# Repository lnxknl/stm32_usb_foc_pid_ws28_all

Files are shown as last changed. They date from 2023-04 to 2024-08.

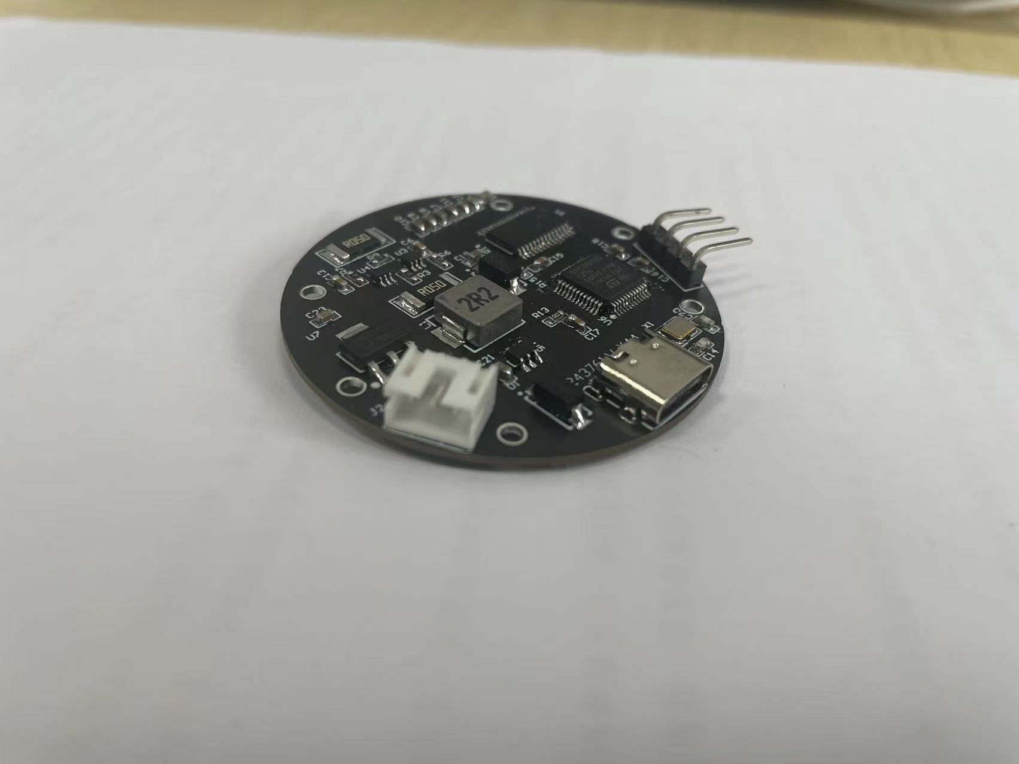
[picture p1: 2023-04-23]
4.Image/pcb侧面图.jpg

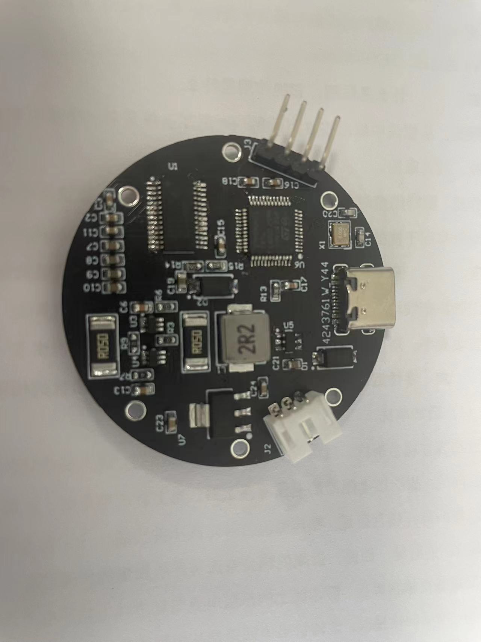
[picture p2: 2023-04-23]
4.Image/pcb正面图.jpg

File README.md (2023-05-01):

**求个START**

## 一. 硬件设计

**主控** : STM32G431CBT6

**稳压芯片**: AMS1117-3.3

**升压芯片**: MT3608(5V升压12V,最大电流支持2A)

**电流采样芯片**: INV199A1DCKR(两相)

**电机驱动芯片**: DRV8313

采用type-c接口供电以及进行usb通讯，2.54弯针接口进行ST-Link下载程序，另外提供了一个PH2.0-3接口(本人用来驱动ws2812)，采用两层板设计。

pcb描述图-反面

pcb描述图-正面

整体图

## 二. 软件设计

##### (1).STM32平台软件设计

###### 1. AS5600参数校准

通过IIC接口读取0x0F和0x0E两个寄存器，可以得到电机的机械角度，此时电机的零角度与AS5600读出的零角度可能不对应，需要进行校准。

将电机旋转到你预想0°的位置，设置foc角度为0°，可以将Ud设置大一点，然后上电，可以看到电机有个微小的偏移，此时读出AS5600的角度值X1，作为**机械角度零偏值**。然后将foc角度设置为90°，上电，再次读出AS5600的角度值X2，那么就可以确定电机的**极对数** = (360 / ((X2 -X1)*4))。电角度和机械角度的转换关系就可以确定下来了。

###### 2. USB协议设计

与PC平台通讯将采用HID复合设备的显示，共两个接口。

第一个为自定义的HID，每个数据包为8bytes，用来进行数据交互。

第二个为HID键盘，配合电机可以发送一些对应的按键，例如: 暂停、切歌、调节音量等等。

##### (2). QT平台软件设计

###### 1. USB协议

采用开源库hidapi进行设计，通过PID和VID锁定设备，然后对接口0进行读写，接口1不管。

###### 2. 串口协议

同样支持通过串口进行交互

###### 2. OpenGL 电机模型

采用OpenGL库读取电机3D模式obj文件，然后将其显示在界面中，与电机旋转位置保持一致。

##### (3).  通讯协议

一个数据包为8字节，首字节恒为0xef，尾字节恒为0xab，中间六个字节为有效数据部分。

###### 1. 公共参数

上位机发送

| 功能码 | 参数码 | 数值4 | 数值3 | 数值2 | 数值1 |
| :----: | :---: | :---: | :---: | :---: | :---: |
|  0x12  | 0x20(运行模式) | 0 | 0 | 0 | 模式 |
|  0x12  | 0x2a(Uq) | float高位 | float低三位 | float低二位 | float低位 |
|  0x12  | 0x2b(Ud) | float高位 | float低三位 | float低二位 | float低位 |
|  0x12  | 0x2c(速度) | float高位 | float低三位 | float低二位 | float低位 |

上位机接收

| 功能码 | 参数码 | 数值4 | 数值3 | 数值2 | 数值1 |
| :----: | :---: | :---: | :---: | :---: | :---: |
|  0x14  | 0x2a(Uq) | float高位 | float低三位 | float低二位 | float低位 |
|  0x14  | 0x2b(Ud) | float高位 | float低三位 | float低二位 | float低位 |
|  0x14  |  0x2c(速度)  | float高位 | float低三位 | float低二位 | float低位 |
|  0x14  |  0x2d(角度)  | float高位 | float低三位 | float低二位 | float低位 |
|  0x14  | 0x2e(Iq电流) | float高位 | float低三位 | float低二位 | float低位 |
|  0x14  | 0x2f(Id电流) | float高位 | float低三位 | float低二位 | float低位 |

##### 2. 位置控制

上位机发送

| 功能码 | 参数码 | 数值4 | 数值3 | 数值2 | 数值1 |
| :----: | :---: | :---: | :---: | :---: | :---: |
|  0x22  | 0x1a(设置角度) | 0 | 0 |  角度高8位  | 角度低8位 |
|  0x22  |  0x1b(设置P) | float高位 | float低三位 | float低二位 | float低位 |
|  0x22  |  0x1c(设置I) | float高位 | float低三位 | float低二位 | float低位 |
|  0x22  |  0x1d(设置D) | float高位 | float低三位 | float低二位 | float低位 |

上位机接收

| 功能码 | 参数码 | 数值4 | 数值3 | 数值2 | 数值1 |
| :----: | :---: | :---: | :---: | :---: | :---: |
|  0x24  | 0x1b(接收P) | float高位 | float低三位 | float低二位 | float低位 |
|  0x24  | 0x1c(接收I) | float高位 | float低三位 | float低二位 | float低位 |
|  0x24  | 0x1d(接收D) | float高位 | float低三位 | float低二位 | float低位 |

##### 3. 开环控制

上位机发送

| 功能码 | 参数码 | 数值4 | 数值3 | 数值2 | 数值1 |
| :----: | :---: | :---: | :---: | :---: | :---: |
|  0x32  | 0x1a(设置运动方向) | 0 | 0 | 0 | 方向(0-顺时针，1-逆时针) |

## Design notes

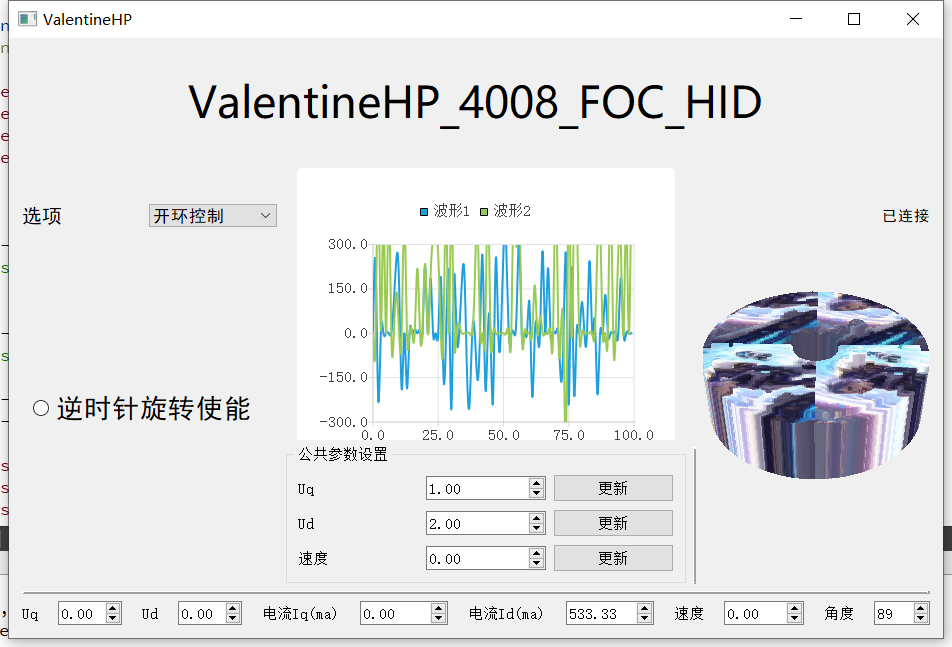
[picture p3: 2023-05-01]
4.Image/上位机.png

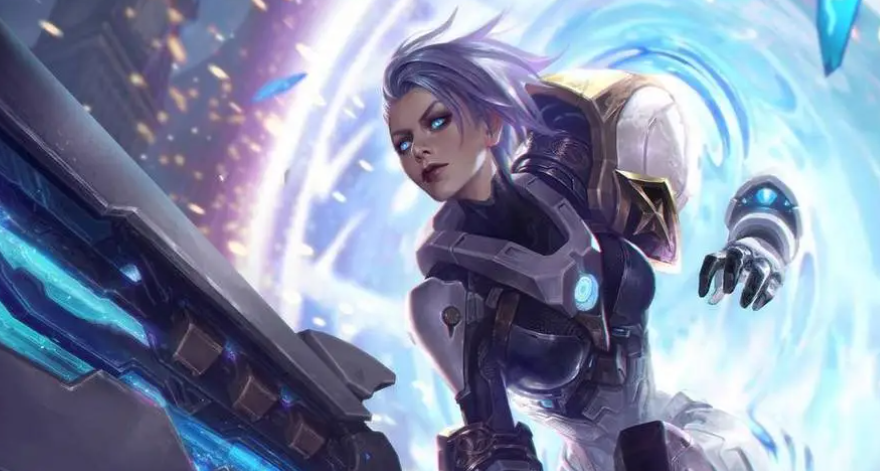
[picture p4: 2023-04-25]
3.Software/QT_FOC_HID/model/tup.png

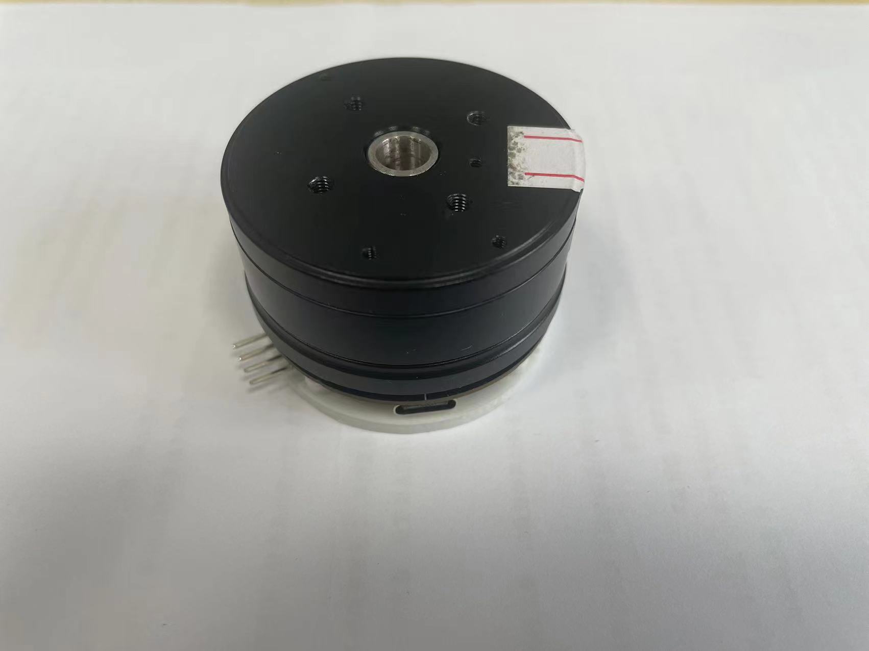
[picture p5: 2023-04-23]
4.Image/整体图.jpg

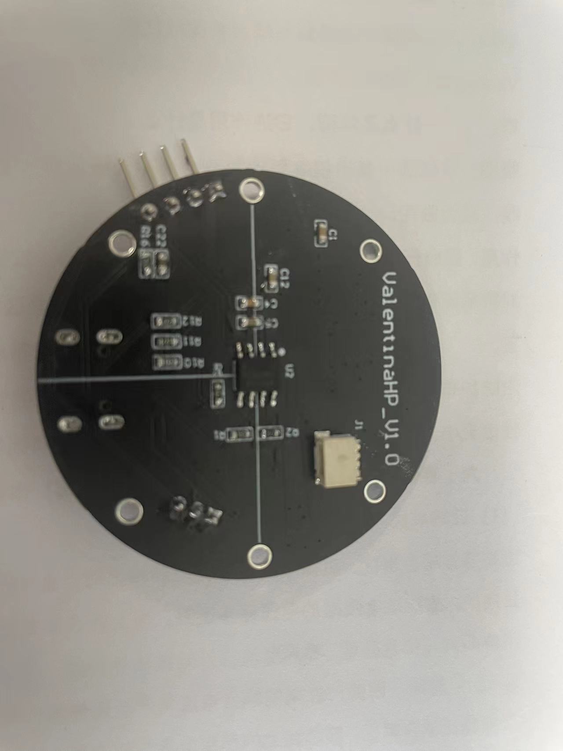
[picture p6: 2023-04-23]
4.Image/pcb背面图.jpg

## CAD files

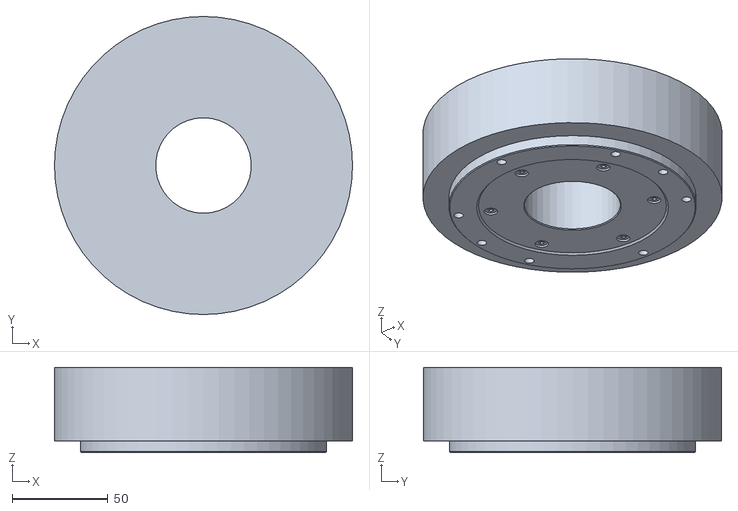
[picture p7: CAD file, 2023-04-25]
2.SolidWorks/SGMCS-04C3C11 - SGMCS-04C3C11.step-1 SGMCS__-4__14N__m-_____04.step.step-1.STL
156.0 x 156.0 x 44.5

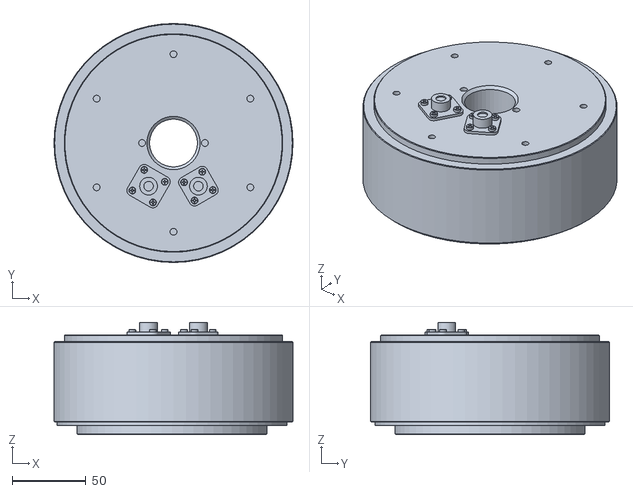
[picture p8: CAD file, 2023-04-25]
3.Software/QT_FOC_HID/model/motor.obj
162.2 x 162.2 x 76.0

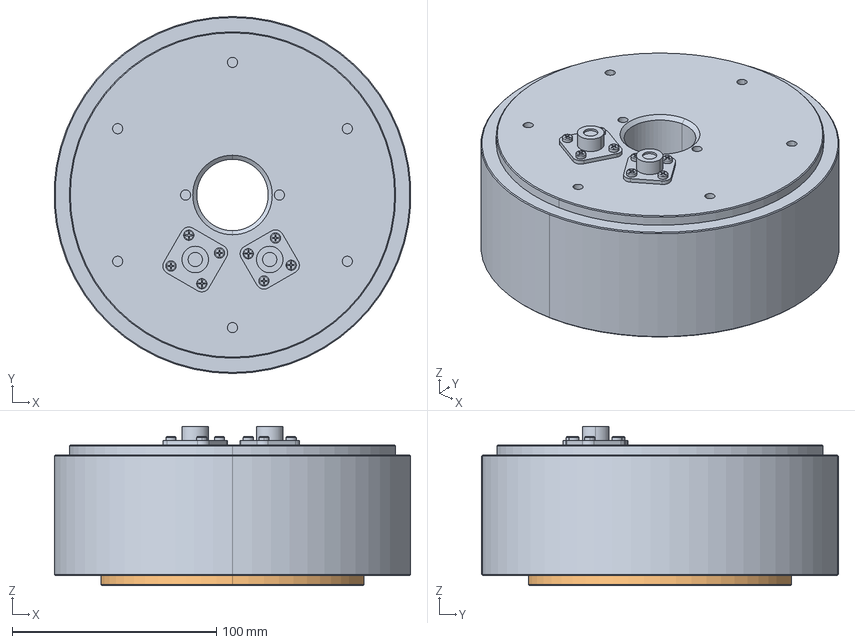
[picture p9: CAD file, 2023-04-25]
2.SolidWorks/SGMCS-04C3C11.step
174.7 x 175.0 x 78.0 mm
SGMCSﾐﾍ-4｡ｫ14N｡､m-ｶｨﾗﾓ_1_04.step
SGMCSﾐﾍ-4｡ｫ14N｡､m-ﾗｪﾗﾓ_04.step

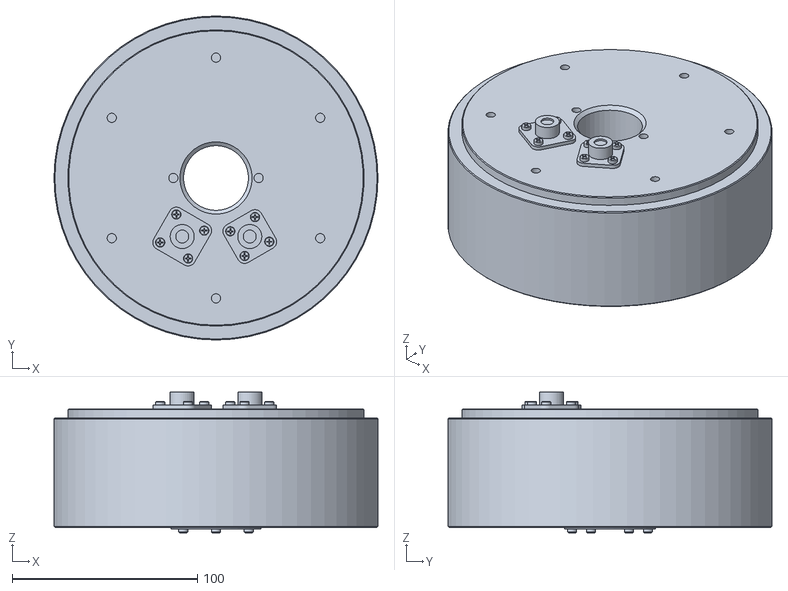
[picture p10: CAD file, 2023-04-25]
2.SolidWorks/SGMCS-04C3C11 - SGMCS-04C3C11.step-1 SGMCS__-4__14N__m-_____1_04.step.step-1.STL
175.0 x 175.0 x 76.0

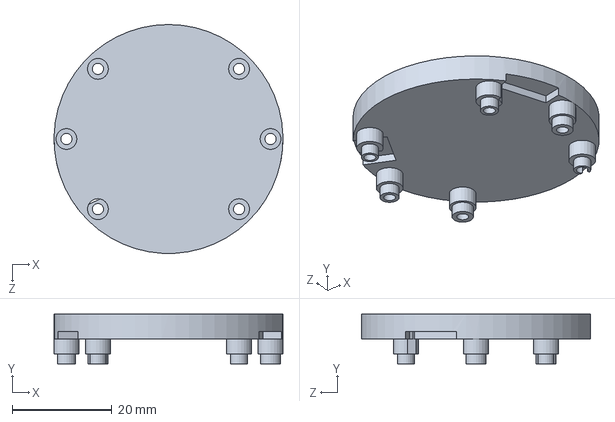
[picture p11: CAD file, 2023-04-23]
2.SolidWorks/4008云台电机外壳.SLDPRT
46.0 x 10.0 x 46.0 mm

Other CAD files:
2.SolidWorks/4008云台电机外壳.STL
2.SolidWorks/SGMCS-04C3C11.SLDASM

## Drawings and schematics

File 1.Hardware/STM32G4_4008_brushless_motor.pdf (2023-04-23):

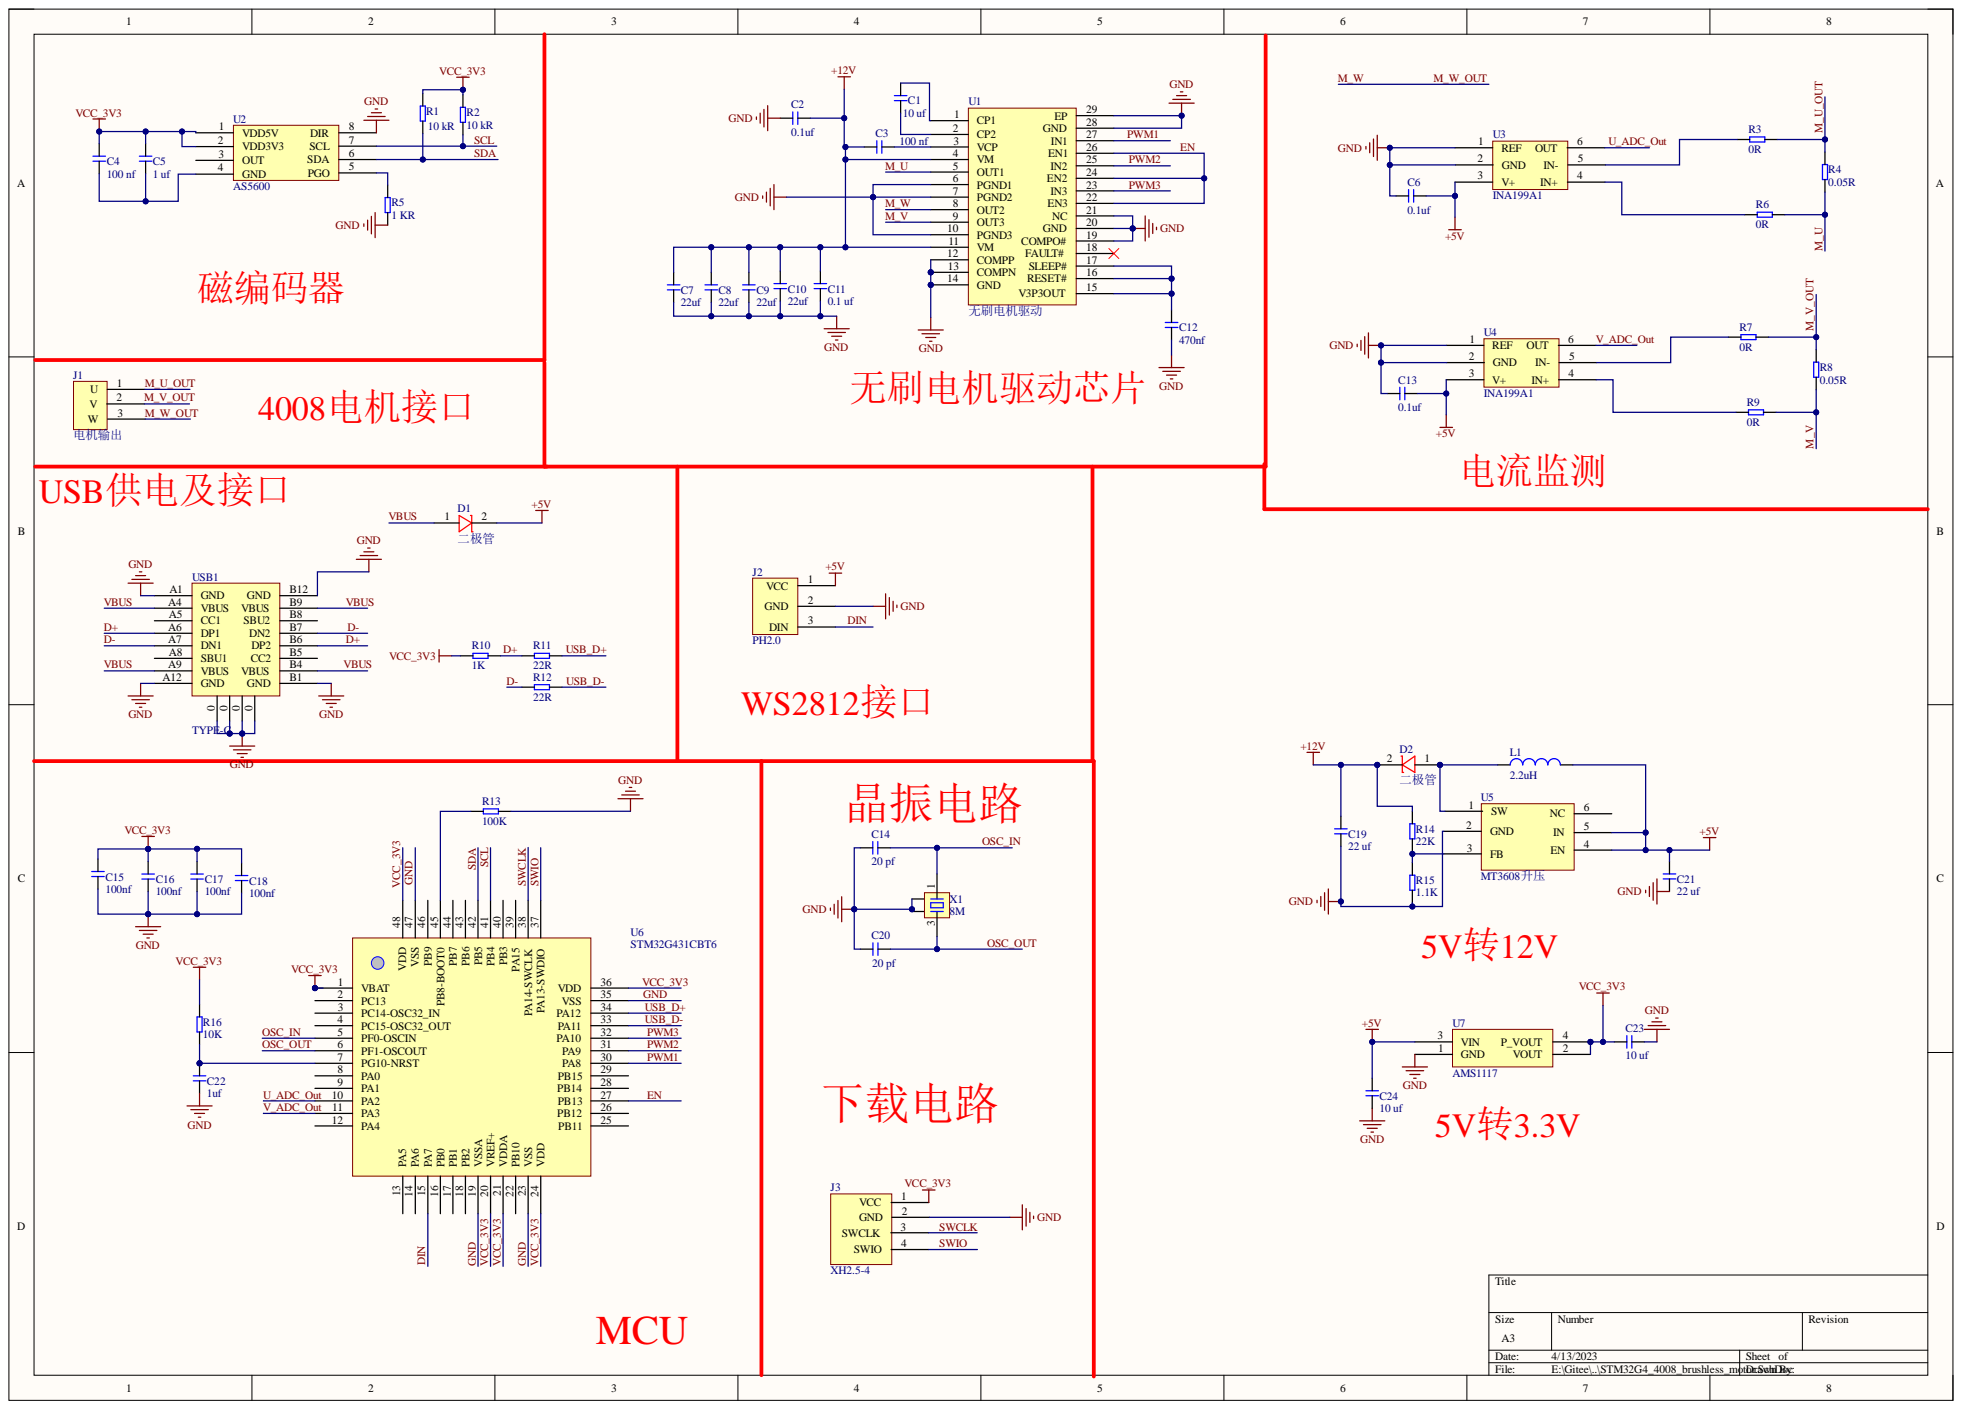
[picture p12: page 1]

PGND1 6 | PWM3
PGND2 7

M_W | OUT2 8

PA13-SWDIO 37 PA14-SWCLK 38 PA15 39 PB3 40 PB4 41 PB5 42 PB6 43 PB7 44 PB8-BOOT0 45 PB9 46 VSS 47 VDD 48

PG10-NRST 7 | PWM1
PA0 8 | EN

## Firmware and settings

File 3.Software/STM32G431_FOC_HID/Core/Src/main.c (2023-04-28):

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
/* Includes ------------------------------------------------------------------*/
#include "main.h"
#include "adc.h"
#include "dma.h"
#include "tim.h"
#include "usart.h"
#include "usb_device.h"
#include "gpio.h"

/* USER CODE BEGIN Includes */
//#include "usbd_cdc_if.h"
/* USER CODE END Includes */

/* USER CODE BEGIN PTD */
#include "common_inc.h"
/* USER CODE END PTD */


void SystemClock_Config(void);
/**
  * @brief  The application entry point.
  * @retval int
  */
int main(void)
{
  /* MCU Configuration--------------------------------------------------------*/

  /* Reset of all peripherals, Initializes the Flash interface and the Systick. */
  HAL_Init();

  /* Configure the system clock */
  SystemClock_Config();

  /* USER CODE BEGIN SysInit */
  GPIO_InitTypeDef GPIO_InitStruct = {0};
  __HAL_RCC_GPIOA_CLK_ENABLE();
  HAL_GPIO_WritePin(GPIOA, GPIO_PIN_12, GPIO_PIN_RESET);
  GPIO_InitStruct.Pin = GPIO_PIN_12;
  GPIO_InitStruct.Mode = GPIO_MODE_OUTPUT_PP;
  GPIO_InitStruct.Pull = GPIO_NOPULL;
  GPIO_InitStruct.Speed = GPIO_SPEED_FREQ_MEDIUM;
  HAL_GPIO_Init(GPIOA, &GPIO_InitStruct);
  HAL_GPIO_WritePin(GPIOA, GPIO_PIN_12, GPIO_PIN_RESET);
  /* USER CODE END SysInit */

  /* Initialize all configured peripherals */
  MX_GPIO_Init();
  MX_DMA_Init();
  MX_USB_Device_Init();
  MX_ADC1_Init();
  MX_TIM1_Init();
  MX_TIM2_Init();
  MX_TIM3_Init();
  MX_USART3_UART_Init();
  /* USER CODE BEGIN 2 */
  HAL_Delay(1000);
  AppMain();
  /* USER CODE END 2 */

  /* Infinite loop */
  /* USER CODE BEGIN WHILE */
  while (1)
  {
    /* USER CODE END WHILE */

    /* USER CODE BEGIN 3 */
  }
  /* USER CODE END 3 */
}

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


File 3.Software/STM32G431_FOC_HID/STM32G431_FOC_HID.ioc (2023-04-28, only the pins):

Mcu.UserName=STM32G431CBTx
PA10.Signal=S_TIM1_CH3
PA11.Signal=USB_DM
PA12.Signal=USB_DP
PA13.Signal=SYS_JTMS-SWDIO
PA14.Signal=SYS_JTCK-SWCLK
PA2.Signal=ADC1_IN3
PA3.Signal=ADC1_IN4
PA7.GPIO_Label=Dout
PA7.Signal=GPIO_Output
PA8.Signal=S_TIM1_CH1
PA9.Signal=S_TIM1_CH2
PB10.Signal=USART3_TX
PB11.Signal=USART3_RX
PB13.GPIO_Label=FOC_Enable
PB13.Signal=GPIO_Output
PB4.GPIO_Label=AS5600_SCL
PB4.Signal=GPIO_Output
PB5.GPIO_Label=AS5600_SDA
PB5.Signal=GPIO_Output
PF0-OSC_IN.Signal=RCC_OSC_IN
PF1-OSC_OUT.Signal=RCC_OSC_OUT

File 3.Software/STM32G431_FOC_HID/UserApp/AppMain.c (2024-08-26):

#include "common_inc.h"
#include "PWM.h"
#include "FOC.h"
#include "electricity_get.h"
#include "USB_HIDCommunication.h"
#include "AS5600.h"
int flag;

int RUNNING_MODE;
int speed_send_flag = 0;
int keyboard_send_cnt = 0;
int keyboard_status = 0;
int nextsong_send_flag = 0;
int revioussong_send_flag = 0;


#define Idle_Mode			0		//空闲
#define Open_Loop_Mode		1		//开环
#define Location_Mode		2		//位置环
#define Moment_Forece_Mode	3		//力矩(电流环)
#define Speed_Mode			4		//速度环
#define HID_KeyBoard_Mode	5		//HID键盘模式(电机为位置环)

void HAL_TIM_PeriodElapsedCallback(TIM_HandleTypeDef *hitm){// @NOTE 
	
	if( hitm == &htim1 )  //更新频率25Khz
	{
		if( flag == 1){
			flag = 0;
			if( RUNNING_MODE == Idle_Mode)
			{	
				pwm_halt();
				return;
			}
			else if(RUNNING_MODE == Open_Loop_Mode)
				open_loop_control();
			else if(RUNNING_MODE == Location_Mode)
				positioning_control();
			else if( RUNNING_MODE == Speed_Mode){
			}
			else if( RUNNING_MODE == HID_KeyBoard_Mode){
					
			}
			 
		}
		else{
			start_adc();
			flag = 1;
		}
			
	}
	if( hitm == &htim3 )  //50khz
	{
		// start_adc();
	}
}
void AppMain(void){
	RUNNING_MODE = Idle_Mode;
	pwm_init();
	foc_init();
	HAL_GPIO_WritePin(GPIOB,GPIO_PIN_13,GPIO_PIN_SET);
	HAL_TIM_Base_Start_IT(&htim1);
	HAL_TIM_Base_Start_IT(&htim2);
	HAL_TIM_Base_Start_IT(&htim3);
	while(1){
		hid_recv_data();
		hid_keyboard_nextsong_send();// @NOTE 
		HAL_Delay(20);
		hid_send_Iq(get_M_Iq());
		HAL_Delay(20);
//		hid_send_Id(get_M_Id());
//		HAL_Delay(1);
//		hid_send_angle(get_as5600_angle());
//		HAL_Delay(1);
//		speed_send_flag += 1;
//		if(speed_send_flag == 15)
//		{
//			speed_send_flag = 0;
//			hid_send_speed(read_as5600_speed());
//		}
//		HAL_Delay(1);
	

}
	
}

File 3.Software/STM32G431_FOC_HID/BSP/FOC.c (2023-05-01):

//
// Created by Valentina_HP on 2023/3/19.
//

#include "FOC.h"
#include "math.h"
#include "USB_HIDCommunication.h"
#include "electricity_get.h"
FOC_Parameter FOC_Parameter_M0;

//Uq = 3  open_loop_speed = 1.2
//Uq = 1.5  open_loop_speed = 0.2
//初始化FOC的一些参数
void foc_init(void){

	
	
	FOC_Parameter_M0.Desire_Ud =0;
	FOC_Parameter_M0.Desire_Uq = 2;
	
	FOC_Parameter_M0.Ts = 1.0;
	FOC_Parameter_M0.Polar_Pair = 11;
	FOC_Parameter_M0.Udc = 12;
	
	
	FOC_Parameter_M0.open_loop_direction = 180;
	FOC_Parameter_M0.open_loop_speed = 0.5;
	
	
	FOC_Parameter_M0.positioning_angle = 0;
}

void Sector_Determination(float u1 , float u2 ,float u3){
    uint8_t  A , B , C , N;
		
		if( u3 > 0 ) A = 1;
	  else A = 0;
		if( u2 > 0 ) B = 1;
	  else B = 0;
		if( u1 > 0 ) C = 1;
	  else C = 0;
    N = 4*C + B * 2 + A;
    if( N == 5)
        FOC_Parameter_M0.sector = 1;
    else if( N == 4)
        FOC_Parameter_M0.sector = 2;
    else if( N == 6)
        FOC_Parameter_M0.sector = 3;
    else if( N == 2)
        FOC_Parameter_M0.sector = 4;
    else if( N == 3)
        FOC_Parameter_M0.sector = 5;
    else
        FOC_Parameter_M0.sector = 6;
}

void Generate_Sector_Time(void){
    float K = ROOT_SIGN_3 * FOC_Parameter_M0.Ts / FOC_Parameter_M0.Udc;
    float U1,U2,U3;
	
    U1 = FOC_Parameter_M0.Ubeta;
    U2 = -0.8660254037844386 * FOC_Parameter_M0.Ualpha - FOC_Parameter_M0.Ubeta/2;
    U3 =  0.8660254037844386* FOC_Parameter_M0.Ualpha - FOC_Parameter_M0.Ubeta/2; 
    Sector_Determination(U1 , U2 ,U3);
    if( FOC_Parameter_M0.sector == 1){
        FOC_Parameter_M0.T4 = K * U3;
        FOC_Parameter_M0.T6 = K * U1;
        if( FOC_Parameter_M0.T4 + FOC_Parameter_M0.T6 > FOC_Parameter_M0.Ts){
            float k = FOC_Parameter_M0.Ts /(FOC_Parameter_M0.T4+ FOC_Parameter_M0.T6) ;
            FOC_Parameter_M0.T4 = k * FOC_Parameter_M0.T4;
            FOC_Parameter_M0.T6 = k * FOC_Parameter_M0.T6;
        }
        FOC_Parameter_M0.T0 = (FOC_Parameter_M0.Ts - FOC_Parameter_M0.T4 - FOC_Parameter_M0.T6) / 2;
        FOC_Parameter_M0.T7 = (FOC_Parameter_M0.Ts - FOC_Parameter_M0.T4 - FOC_Parameter_M0.T6) / 2;
    }
    else if(FOC_Parameter_M0.sector == 2 ){
        FOC_Parameter_M0.T2 = -K * U3;
        FOC_Parameter_M0.T6 = -K * U2;
        if( FOC_Parameter_M0.T2 + FOC_Parameter_M0.T6 > FOC_Parameter_M0.Ts){
            float k = FOC_Parameter_M0.Ts /(FOC_Parameter_M0.T2+ FOC_Parameter_M0.T6) ;
            FOC_Parameter_M0.T2 = k * FOC_Parameter_M0.T2;
            FOC_Parameter_M0.T6 = k * FOC_Parameter_M0.T6;
        }
        FOC_Parameter_M0.T0 = (FOC_Parameter_M0.Ts - FOC_Parameter_M0.T2 - FOC_Parameter_M0.T6) / 2;
        FOC_Parameter_M0.T7 = (FOC_Parameter_M0.Ts - FOC_Parameter_M0.T2 - FOC_Parameter_M0.T6) / 2;
    }
    else if(FOC_Parameter_M0.sector == 3){
        FOC_Parameter_M0.T2 = K * U1;
        FOC_Parameter_M0.T3 = K * U2;
        if( FOC_Parameter_M0.T2 + FOC_Parameter_M0.T3 > FOC_Parameter_M0.Ts){
            float k = FOC_Parameter_M0.Ts /(FOC_Parameter_M0.T2+ FOC_Parameter_M0.T3) ;
            FOC_Parameter_M0.T2 = k * FOC_Parameter_M0.T2;
            FOC_Parameter_M0.T3 = k * FOC_Parameter_M0.T3;
        }
        FOC_Parameter_M0.T0 = (FOC_Parameter_M0.Ts - FOC_Parameter_M0.T2 - FOC_Parameter_M0.T3) / 2;
        FOC_Parameter_M0.T7 = (FOC_Parameter_M0.Ts - FOC_Parameter_M0.T2 - FOC_Parameter_M0.T3) / 2;
    }
    else if(FOC_Parameter_M0.sector == 4){
        FOC_Parameter_M0.T1 = -K * U1;
        FOC_Parameter_M0.T3 = -K * U3;
        if( FOC_Parameter_M0.T1 + FOC_Parameter_M0.T3 > FOC_Parameter_M0.Ts){
            float k = FOC_Parameter_M0.Ts /(FOC_Parameter_M0.T1+ FOC_Parameter_M0.T3) ;
            FOC_Parameter_M0.T1 = k * FOC_Parameter_M0.T1;
            FOC_Parameter_M0.T3 = k * FOC_Parameter_M0.T3;
        }
        FOC_Parameter_M0.T0 = (FOC_Parameter_M0.Ts - FOC_Parameter_M0.T1 - FOC_Parameter_M0.T3) / 2;
        FOC_Parameter_M0.T7 = (FOC_Parameter_M0.Ts - FOC_Parameter_M0.T1 - FOC_Parameter_M0.T3) / 2;
    }
    else if(FOC_Parameter_M0.sector == 5){
        FOC_Parameter_M0.T1 = K * U2;
        FOC_Parameter_M0.T5 = K * U3;
        if( FOC_Parameter_M0.T1 + FOC_Parameter_M0.T5 > FOC_Parameter_M0.Ts){
            float k = FOC_Parameter_M0.Ts /(FOC_Parameter_M0.T1+ FOC_Parameter_M0.T5) ;
            FOC_Parameter_M0.T1 = k * FOC_Parameter_M0.T1;
            FOC_Parameter_M0.T5 = k * FOC_Parameter_M0.T5;
        }
        FOC_Parameter_M0.T0 = (FOC_Parameter_M0.Ts - FOC_Parameter_M0.T1 - FOC_Parameter_M0.T5) / 2;
        FOC_Parameter_M0.T7 = (FOC_Parameter_M0.Ts - FOC_Parameter_M0.T1 - FOC_Parameter_M0.T5) / 2;
    }
    else {
        FOC_Parameter_M0.T4 = -K * U2;
        FOC_Parameter_M0.T5 = -K * U1;
        if( FOC_Parameter_M0.T4 + FOC_Parameter_M0.T5 > FOC_Parameter_M0.Ts){
            float k = FOC_Parameter_M0.Ts /(FOC_Parameter_M0.T4+ FOC_Parameter_M0.T5) ;
            FOC_Parameter_M0.T4 = k *FOC_Parameter_M0. T4;
            FOC_Parameter_M0.T5 = k *FOC_Parameter_M0.T5;
        }
        FOC_Parameter_M0.T0 = (FOC_Parameter_M0.Ts - FOC_Parameter_M0.T4 - FOC_Parameter_M0.T5) / 2;
        FOC_Parameter_M0.T7 = (FOC_Parameter_M0.Ts - FOC_Parameter_M0.T4 - FOC_Parameter_M0.T5) / 2;
    }

}
void Generate_SVPWM(void){
	float Ta , Tb , Tc;
    if( FOC_Parameter_M0.sector == 1){
        Ta = FOC_Parameter_M0.T4 + FOC_Parameter_M0.T6 + FOC_Parameter_M0.T7;
        Tb = FOC_Parameter_M0.T6 + FOC_Parameter_M0.T7;
        Tc = FOC_Parameter_M0.T7;
    }
    else if( FOC_Parameter_M0.sector == 2){
        Ta = FOC_Parameter_M0.T6 + FOC_Parameter_M0.T7;
        Tb = FOC_Parameter_M0.T2 + FOC_Parameter_M0.T6 + FOC_Parameter_M0.T7;
        Tc = FOC_Parameter_M0.T7;
    }
    else if( FOC_Parameter_M0.sector == 3){
        Ta = FOC_Parameter_M0.T7;
        Tb = FOC_Parameter_M0.T2 + FOC_Parameter_M0.T3 + FOC_Parameter_M0.T7;
        Tc = FOC_Parameter_M0.T3 + FOC_Parameter_M0.T7;
    }
    else if( FOC_Parameter_M0.sector == 4){
        Ta = FOC_Parameter_M0.T7;
        Tb = FOC_Parameter_M0.T3 + FOC_Parameter_M0.T7;
        Tc = FOC_Parameter_M0.T1 + FOC_Parameter_M0.T3 + FOC_Parameter_M0.T7;
    }
    else if( FOC_Parameter_M0.sector == 5){
        Ta = FOC_Parameter_M0.T5 + FOC_Parameter_M0.T7;
        Tb = FOC_Parameter_M0.T7;
        Tc = FOC_Parameter_M0.T1 + FOC_Parameter_M0.T5 + FOC_Parameter_M0.T7;
    }
    else{
        Ta = FOC_Parameter_M0.T4 + FOC_Parameter_M0.T5 + FOC_Parameter_M0.T7;
        Tb = FOC_Parameter_M0.T7;
        Tc = FOC_Parameter_M0.T5 + FOC_Parameter_M0.T7;
    }
    pwm_update(Ta,Tb,Tc);
}

void cal_angle_sincos(){
	float angle = FOC_Parameter_M0.angle  * 0.0174532922222;
	FOC_Parameter_M0.cosVal =  cos(angle);
	FOC_Parameter_M0.sinVal =  sin(angle);
}

void Clarke(){
	FOC_Parameter_M0.Ialpha =  FOC_Parameter_M0.currU;
	FOC_Parameter_M0.Ibeta  = (FOC_Parameter_M0.currU + 2*FOC_Parameter_M0.currV) *  0.5773502692f;
}
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

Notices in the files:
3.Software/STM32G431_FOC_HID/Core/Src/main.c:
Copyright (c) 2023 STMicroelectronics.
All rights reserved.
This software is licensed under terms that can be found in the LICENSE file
